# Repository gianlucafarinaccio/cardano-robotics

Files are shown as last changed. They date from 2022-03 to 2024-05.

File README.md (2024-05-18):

# CardanoRobotics



This repository is a brief presentation of CardanoRobotics, RobocupJunior Soccer Open team from **IIS P.zza della Resistenza** (previously known as ITIS G. Cardano Institute), Rome.
CardanoRobotics represented Italy at **RobocupJunior2019, Sydney** in July 2019 after the victory at **Italian Championship 2019** in April.

#### Results and partecipations in national and international competitions:
- Romecup 2018, 5th place in Soccer Open League
- Romecup 2019, 1st place in Soccer Open League
- RoboCup 2019, 11th place in Soccer Open League

#### Team was made up by:
- Gianluca Farinaccio -- Leader , Software
- Daniele Galli -- Hardware
- Matteo Persichetti -- Mechanics
- Francesco Tocci -- Software
- Simone Vasta -- Hardware

#### Some specs about our last-generation of robots:
- Camera: OpenMV Cam H7/M7;
- 4 x VLX530x ToF handled by 4 x ;
- ToF controller: 4 x PIC16F series microcontroller
- Main controller: 1 x  Microchip PIC18f87k22;
- Slave controller: 1 x Microchip PIC18f26k22 to handle Line sensors;

> All materials contained in this repo was designed and made by 18 years old students minds.\
> This is a very very small part of all materials made in over 2.5 years of work and represent 
> the final status of our robots, before the end of the project in September 2019.\
> All good things got an end.
> Big thanks to all team and RoboCup members for all good vibes and memories gave to me. \
> Made with love, from Rome to Sydney. <3

###### if you want to know more about RoboCup
https://junior.robocup.org \
http://www.robocupjunior.it \
https://www.robocup.org

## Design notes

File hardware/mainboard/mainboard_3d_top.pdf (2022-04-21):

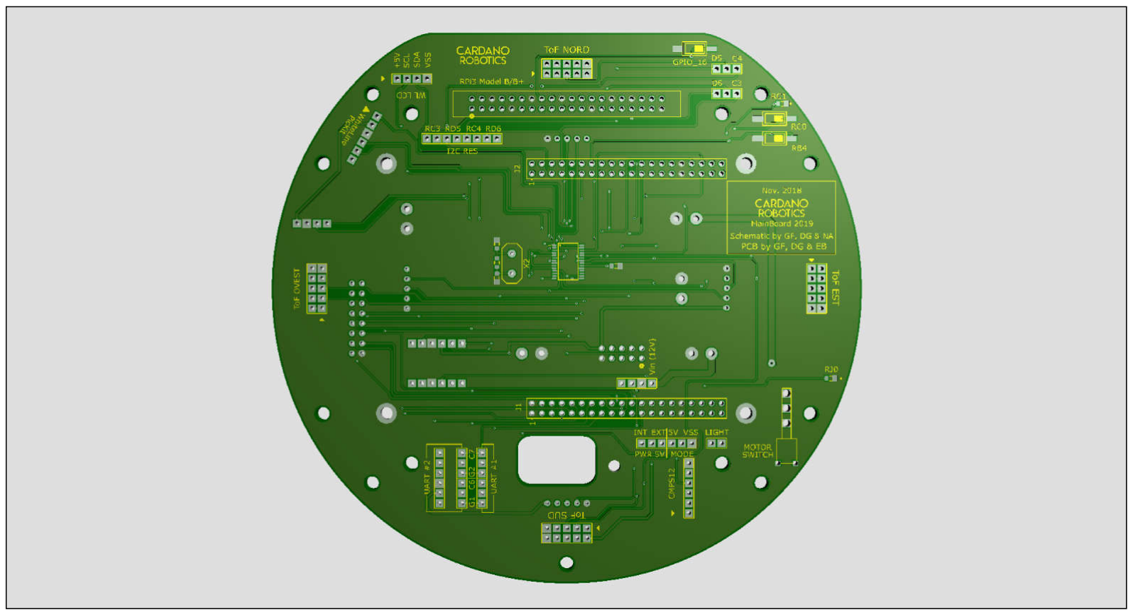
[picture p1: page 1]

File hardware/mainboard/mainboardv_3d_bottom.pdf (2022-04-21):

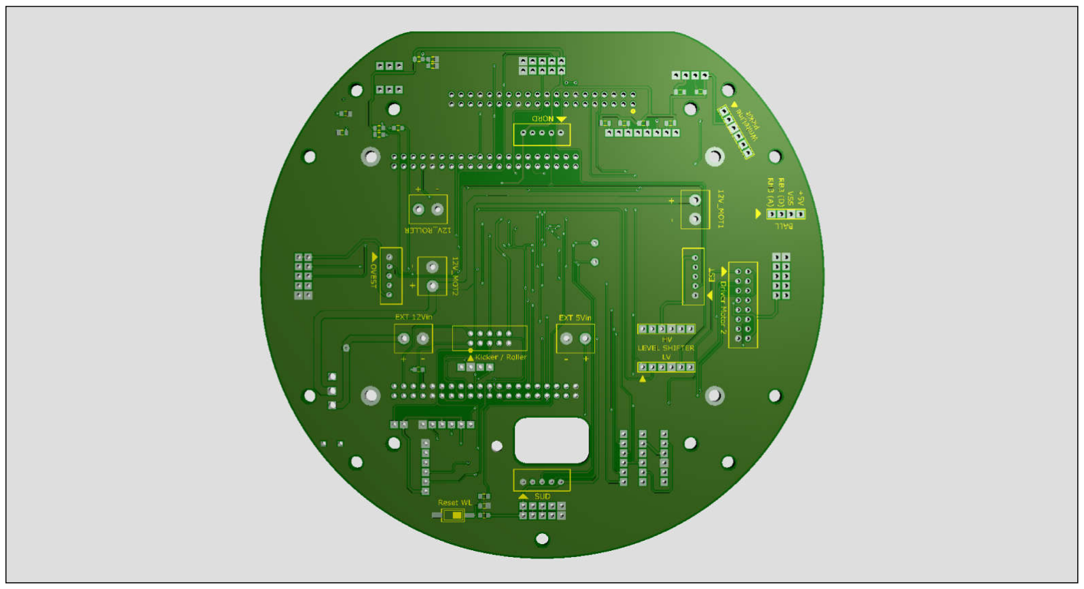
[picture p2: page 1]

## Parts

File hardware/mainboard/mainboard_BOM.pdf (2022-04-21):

## Bill Of Materials for Mainboard v1.0n

Design Title | Mainboard v1.0n

### Author Document Number Revision

Design Created | giovedì 6 settembre 2018
Design Last Modified domenica 11 novembre 2018

### Total Parts In Design 70

### 0 Modules

Quantity | References | Value | PCB Package
Sub-totals:

### 7 Capacitors

Quantity | References | Value | PCB Package
5 | C1,C2,C4,C5,C7 | 100nF | 0805_CAP
2 | C3,C6 | 18pF | 0805_CAP
Sub-totals:

### 15 Resistors

Quantity | References | Value | PCB Package
9 | R1,R2,R5,R11,R14,R15,R18,R19,R20 | 2k2 | 0805_RES
1 | R3 | 18k | 0805_RES
1 | R7 | 47k | 0805_RES
1 | R8 | 100 | 0805_RES
1 | R9 | 10M | 0805_RES
2 | R10,R12 | 330 | 0805_RES
Sub-totals:

### 1 Integrated Circuits

Quantity | References | Value | PCB Package
1 | U2 | PIC18F25K42 | SSOP28
Sub-totals:

### 0 Transistors

Quantity | References | Value | PCB Package
Sub-totals:

### 2 Diodes

Quantity | References | Value | PCB Package
1 | D3 | LED | 0805
1 | D5 | USR_LED | 0805
Sub-totals:

### 45 Miscellaneous

Quantity | References | Value | PCB Package
1 | BUTTON1 | USR_BUTTON1 | BUTTON_A
1 | BUTTON2 | USR_BUTTON2 | BUTTON_A
1 | BUTTON3 | USR_BUTTON3 | BUTTON_A
1 | BUTTON4 | RESET_LINE | BUTTON_A
2 | J1,J2 | anxaPic80v4.1 Conn | CON40_2X20
1 | J3 | RPi 3 Model B/B+ Conn | CON40_2X20_US_FCI
1 | J4 | CONN_CMPS12 | CONN-SIL6
1 | J5 | Motor Driver Conn2 | TRANS 16 DIL
1 | J6 | CONN-SIL4 | CONN-SIL4
1 | J7 | TOFN_Conn | CONN-DIL10
1 | J8 | TOFS_Conn | CONN-DIL10
1 | J9 | TOFE_Conn | CONN-DIL10
1 | J10 | TOFO Conn | CONN-DIL10
1 | J11 | Conn_WhiteLine_NORD | XH-JST_CONNECTOR_5
1 | J12 | Conn_WhiteLine_SUD | XH-JST_CONNECTOR_5
1 | J13 | Conn_WhiteLine_EST | XH-JST_CONNECTOR_5
1 | J14 | Conn_WhiteLine_OVEST | XH-JST_CONNECTOR_5
1 | J15 | PICKIT_WL | CONN-SIL6
1 | J16 | LCD_WL | CONN-SIL4
1 | J18 | CONN_BALL | CONN-SIL4
1 | J19 | Kicker/Roller | CON10_2X5_US_FCI
1 | J21 | RS232/Bluetooth | CONN-SIL6
1 | J23 | EXT 12Vin | TBLOCK-M2
1 | J25 | 12V_MOT2 | TBLOCK-M2
1 | J26 | 12V_ROLLER | TBLOCK-M2
1 | J27 | 12V_MOT1 | TBLOCK-M2

1 | J28 | EXT 5Vin | TBLOCK-M2 1 | J29 | LV | CONN-SIL6 1 | J30 | HV | CONN-SIL6 1 | JP1 | JUMPER | CONN-SIL2 1 | JP4 | RS232#1 TX | CONN-SIL3 1 | JP5 | RS232#1 RX | CONN-SIL3 1 | JP6 | CONN1 | CONN-SIL3 1 | JP7 | RS232#2 RX | CONN-SIL3 1 | JP8 | SDA_I2C | CONN-SIL3 1 | JP9 | SCL_I2C | CONN-SIL3 1 | JP10 | CMPS_MODE | CONN-SIL3 1 | JP11 | RC3 | CONN-SIL2 1 | JP12 | RC4 | CONN-SIL2 1 | JP13 | RD5 | CONN-SIL2 1 | JP14 | RD6 | CONN-SIL2 1 | JP17 | 5V INT / 5V EXT | CONN-SIL3 1 | SW2 | SWITCH_MOTOR | VERT_SPDT 1 | X2 | 8 MHz | XTAL18

Sub-totals:

Totals:

domenica 11 novembre 2018 13:12:40

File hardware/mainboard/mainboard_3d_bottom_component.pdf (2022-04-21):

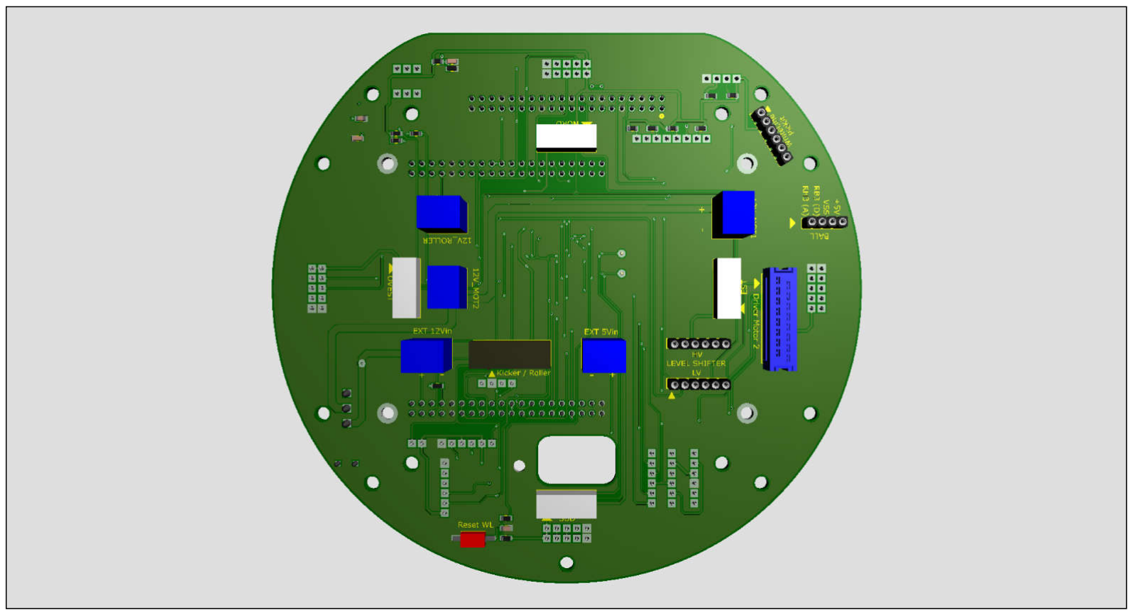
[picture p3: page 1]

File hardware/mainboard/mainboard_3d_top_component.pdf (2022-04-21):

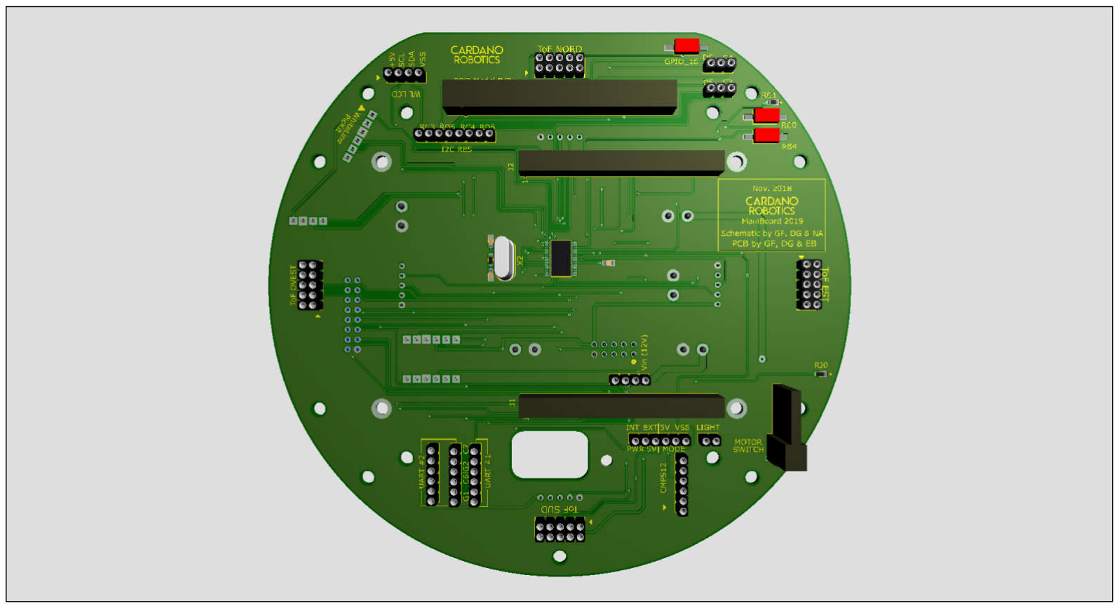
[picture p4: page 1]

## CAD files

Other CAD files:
mechanics/RobotSydney.dwg

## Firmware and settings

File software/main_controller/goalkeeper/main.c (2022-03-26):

#include <main.h>
#include <Drv4Mot2019_v1.c>
#include <RoboFunctions_v5p.c>


#INT_EXT2
void  EXT2_isr(void) {
   WlRilevata = True;
   disable_interrupts(INT_EXT2);

}

#INT_RDA2
void  RDA2_isr(void) {
   AllData = SerialRoutine();
}


void main() {
   MotorInit();
   RoboSetup();

   while(TRUE){

     if(WlRilevata){
        robo.Line.DataByte = Line_Read(0x18);
        if(robo.Line.DataByte==0 ||robo.Line.DataByte==255){
           Dir(0,0,VERSONORD);
           robo.Line.BallOut = False;
        } else{
           robo.Line.LineRoutineDir = LineRoutine(robo.Line.DataByte);
           Dir(1.35,robo.Line.LineRoutineDir,VERSONORD);
           robo.Line.BallOut = True;
        }
           WlRilevata = False;
           clear_interrupt(INT_EXT2);
           enable_interrupts(INT_EXT2);
     } else{
         robo.ToF.sud = ToF_Read(0x16);
         if(!robo.Line.BallOut){
               robo.Line.BallOut=False;
               if((robo.ToF.sud>25) && (robo.Goal.kick==False)){
                  OnGoal(1.35,robo.Goal.gdegrees);
               } else{
                  if(robo.Ball.bdegrees != 999 && robo.Line.BallOut==0){
                     if(((robo.Ball.bdegrees<20||robo.Ball.bdegrees>340)&&(robo.ToF.sud<210))||((robo.Ball.bdistance<40)&&(robo.Ball.bdegrees<20||robo.Ball.bdegrees>340))){
                        Dir(1.35,0,VERSONORD);
                        robo.Goal.kick=True;
                     } else{
                         robo.Goal.kick=False;
                         if(robo.Ball.bdegrees<=180){ Dir(1.3,90,VERSONORD); }
                         else{ Dir(1.3,270,VERSONORD); }
                       }
                  } else{
                     robo.Goal.kick=False;
                     if(robo.Goal.gdegrees>190||robo.Ball.bdegrees<170){
                        if(robo.Goal.gdegrees<=180){ Dir(1.35,90,VERSONORD); }
                        else{ Dir(1.35,270,VERSONORD); }
                     } else{
                          Dir(0,0,VERSONORD);
                     }
                  }
               }

         } else{
            if(robo.Goal.gdegrees>190||robo.Goal.gdegrees<170){
               robo.Line.BallOut=True;
               ReturnGoal(1.35,robo.Goal.gdegrees);
            } else{
                  robo.Line.BallOut=False;
                  Dir(0,0,0);
            }
         }




      }
   } //end loop
} //end main

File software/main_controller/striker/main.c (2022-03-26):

#include <main.h>
#include <Drv4Mot2019_v1.c>
#include <RoboFunctions_v7.c>


#INT_EXT2
void  EXT2_isr(void) {
   WlRilevata = True;
   disable_interrupts(INT_EXT2);
}

#INT_RDA2
void  RDA2_isr(void) {
   AllData = SerialRoutine();
}

#INT_RTCC
void  RTCC_isr(void) {
   output_toggle(ROLLER);
   level==1? set_rtcc(25535+tHigh):set_rtcc(25535+tLow);
   level = !level;
   initRoller<100? initRoller++: 100;
}

#INT_TIMER1
void  TIMER1_isr(void) {
   static int8 kickStep=0;

   if(kickStep==0){
      output_low(KICKER);
      kickStep+=1;
      set_timer1(65536-(msOverflow*1000));
   } else{
      if(kickStep>0 && kickStep<10){
         set_timer1(65536-(msOverflow*1000));
         kickStep+=1;
      } else{
         kickAvaible = 1;
         kickStep = 0;
         disable_interrupts(INT_TIMER1);
      }
   }
}

void main() {
   MotorInit();
   RoboSetup();
     /* SETUP ESC FOR ROLLER */
    setup_timer_0(RTCC_INTERNAL|RTCC_DIV_4);      //32,7 ms overflow //0.5us
    setup_esc(500);
    enable_interrupts(INT_RTCC);
    enable_interrupts(GLOBAL);
    while(initRoller<20);
    setup_esc(500);

   while(TRUE){

     if(WlRilevata){
        robo.Line.DataByte = Line_Read(0x18);
        if(robo.Line.DataByte==0 ||robo.Line.DataByte==255){
           Dir(0,0,VERSONORD);
           robo.Line.BallOut = False;
        } else{

           robo.Line.LineRoutineDir = LineRoutine(robo.Line.DataByte);
           Dir(1.2,robo.Line.LineRoutineDir,VERSONORD);
           robo.Line.BallOut = True;
        }
           WlRilevata = False;
           //clear_interrupt(INT_EXT2);
           enable_interrupts(INT_EXT2);
     } else{

       control_roller();
       control_kicker();

       if(!robo.Line.BallOut){
          robo.Line.BallOut = False;
          if(robo.goal.gdegrees!=999 && robo.ball.bvalue>=5){
              OnGoal(1.2,robo.goal.gdegrees);
          } else{
              OnBall(1.2,robo.Ball.bdegrees);
          }

       } else{
             if((!BallOutRange(robo.Line.OutLineAngle))&&(robo.Ball.bdegrees!=999)){
                robo.Line.BallOut = True;
                followOutBall(robo.Line.OutLineAngle);
             } else{ //una delle condizioni sopra non e' verificata
                   robo.Line.BallOut = False;
                   OnBall(1.2,robo.Ball.bdegrees);
             }
        }
     }

   } //end loop
} //end main
